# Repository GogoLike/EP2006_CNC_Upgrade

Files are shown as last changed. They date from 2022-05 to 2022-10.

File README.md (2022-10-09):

View this project on [CADLAB.io](https://cadlab.io/project/25653). 

## EP2006_CNC_Upgrade Project

# Описание проекта

Проект заключается в модернизации фрезерно-гравировально-сверлильного станка EP2006.
В качестве мождернизации подразумевается переход управления на стандарт G-Code с контроллером на открытой прошивке GRBL.
Контроллером в новой плате является STM32F103 в составе платы BluePill.

# Текущее состояние проекта

*Интерфейсы:*
- Известно управление исходным частотным преобразователем шпинделя
- Известно управление 5-ти фазными шаговыми двигателями через исходные драайвера шаговых двигателей осей X и Y
- Известно управление 2-х фазным шаговым двигателем через исходный драйвер шагового двигателя оси Z

*Датчики:*
- Известно подключение датчиков HOME
- Известно подключение датчика PROBE
- Выбрано подключение кнопки паузы на сигнал SAFETY_DOOR
- Выбрано подключение реле пылеососа на сигнал SPINDEL_ENABLE

*Схемотехника:*
- Коннектор для BluePill
- Датчики HOME заведены через оптопары и ферритовые кольца
- Управление X Y заведено через драйвер дифф. линий SN75ALS192N
- Управление Z заведено через инвертор SN7406N
- На Disable Steppers заведено только Enable Z

*PCB:*
- Реализовано на макетной плате

*Прошивка:*
- Удалось прошить контроллер
- В процессе настройки
- Проверена работоспособность движения по осям и перехода в HOME
- Проверен функционал щупа
- Проверено включение шпинделя
- Проверена резка плат

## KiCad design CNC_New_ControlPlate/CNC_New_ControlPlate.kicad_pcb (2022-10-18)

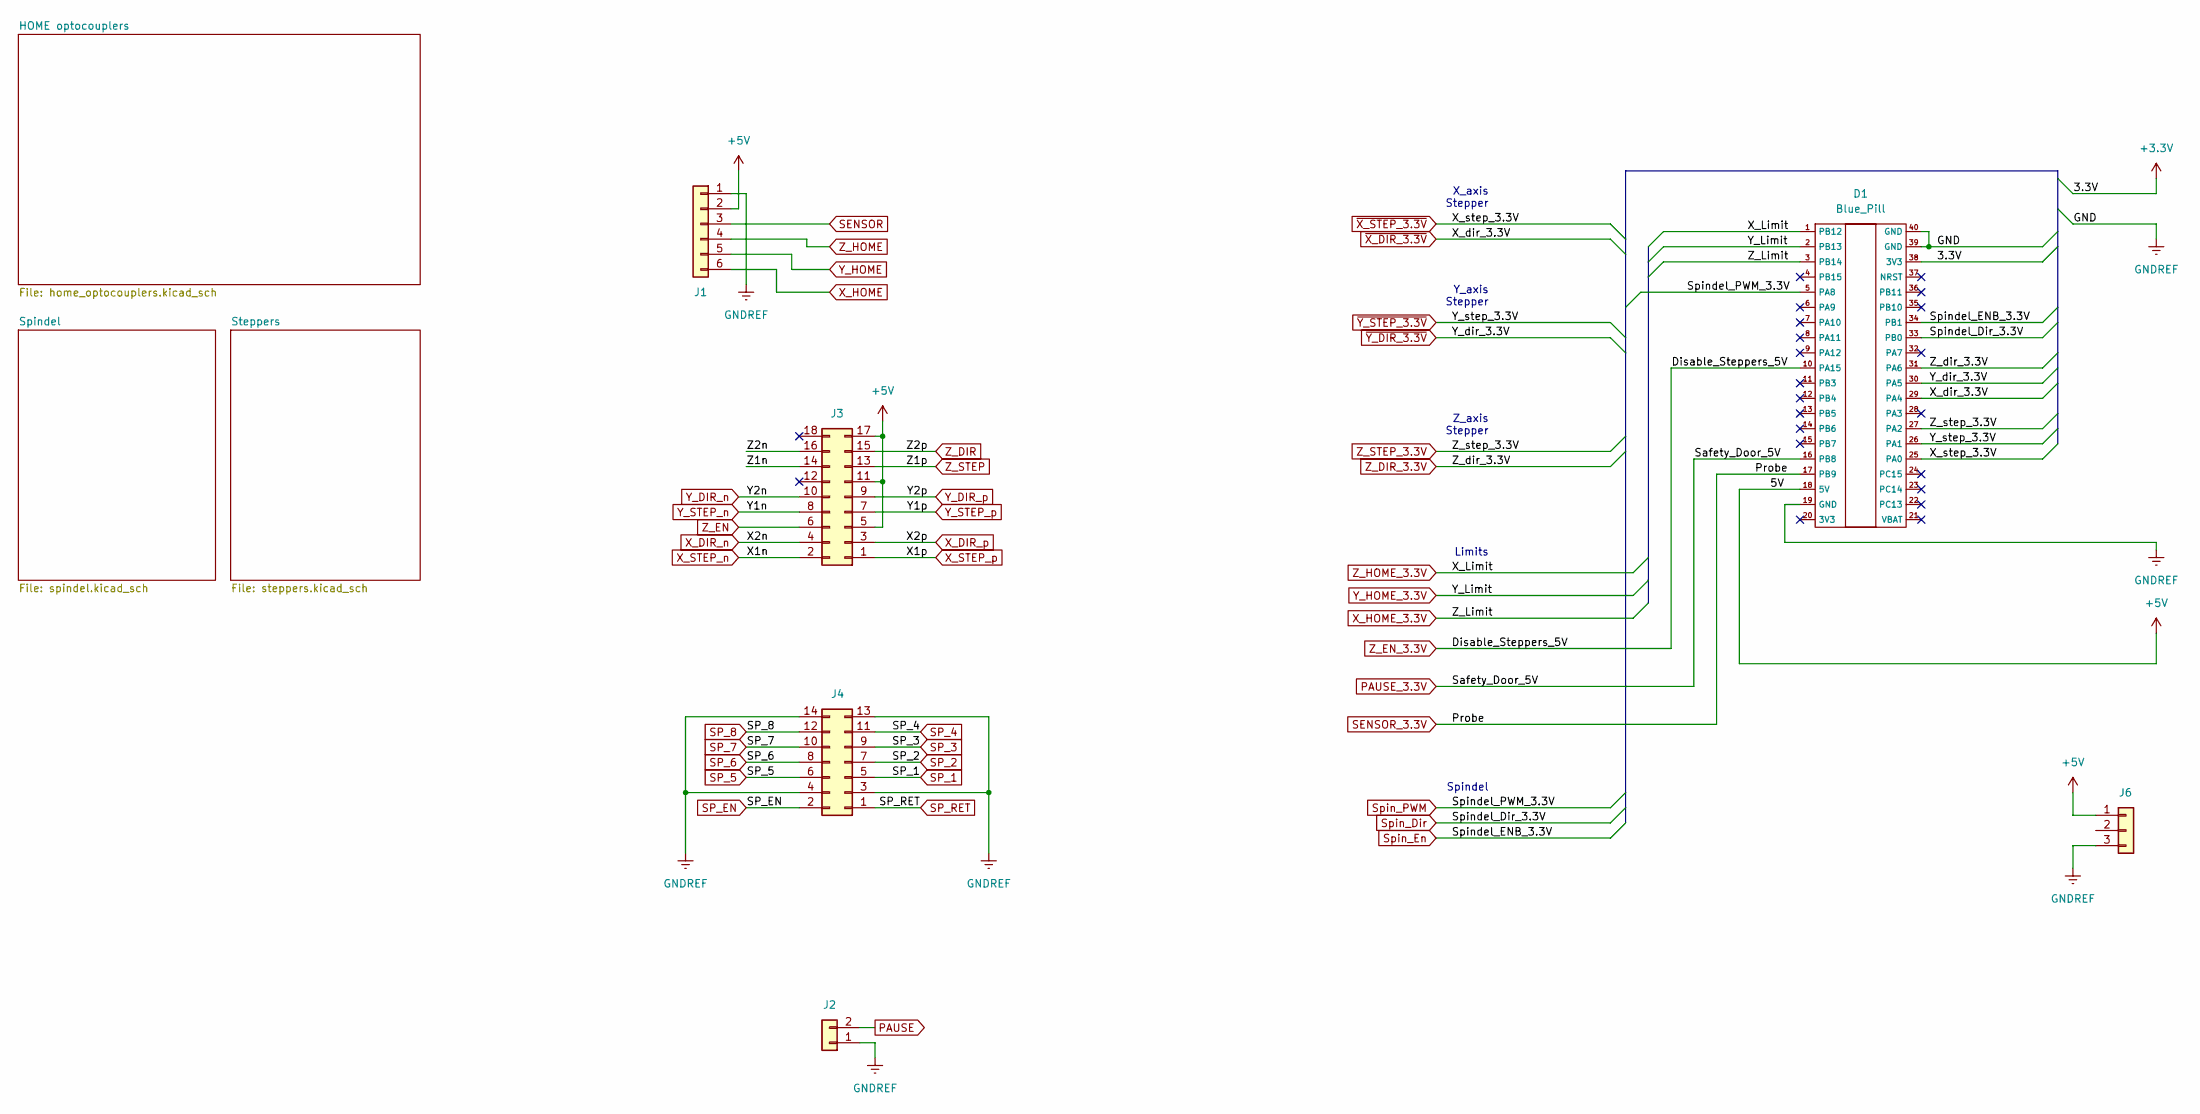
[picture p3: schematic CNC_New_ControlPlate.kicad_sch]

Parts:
D1: Blue_Pill; Maple_Mini
J1: OTHER; JST_XH_B6B-XH-A_1x06_P2.50mm_Vertical
J2: Conn_01x02; JST_XH_B2B-XH-A_1x02_P2.50mm_Vertical
J3: STEPPERS; PinHeader_2x09_P2.54mm_Vertical
J4: SPINDEL; PinHeader_2x07_P2.54mm_Vertical
J6: Conn_01x03; JST_VH_B3P-VH_1x03_P3.96mm_Vertical

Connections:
+3V3: D1.38 (3V3); also elsewhere on the board
+5V: D1.18 (5V), J1.2, J3.5, J3.11, J3.17, J6.1; also elsewhere on the board
/Z1n: J3.14
/Z2n: J3.16
GNDREF: D1.19 (GND), D1.39 (GND), D1.40 (GND), J1.1, J2.1, J4.3, J4.4, J4.13, J4.14, J6.3; also elsewhere on the board
PAUSE: J2.2; also elsewhere on the board
PAUSE_3.3V: D1.16 (PB8); also elsewhere on the board
SENSOR: J1.3; also elsewhere on the board
SENSOR_3.3V: D1.17 (PB9); also elsewhere on the board
SP_1: J4.5; also elsewhere on the board
SP_2: J4.7; also elsewhere on the board
SP_3: J4.9; also elsewhere on the board
SP_4: J4.11; also elsewhere on the board
SP_5: J4.6; also elsewhere on the board
SP_6: J4.8; also elsewhere on the board
SP_7: J4.10; also elsewhere on the board
SP_8: J4.12; also elsewhere on the board
SP_EN: J4.2; also elsewhere on the board
SP_RET: J4.1
Spin_Dir: D1.33 (PB0)
Spin_En: D1.34 (PB1); also elsewhere on the board
Spin_PWM: D1.5 (PA8); also elsewhere on the board
X_DIR_n: J3.4; also elsewhere on the board
X_DIR_p: J3.3; also elsewhere on the board
X_HOME: J1.6; also elsewhere on the board
X_HOME_3.3V: D1.3 (PB14); also elsewhere on the board
X_STEP_n: J3.2; also elsewhere on the board
X_STEP_p: J3.1; also elsewhere on the board
Y_DIR_n: J3.10; also elsewhere on the board
Y_DIR_p: J3.9; also elsewhere on the board
Y_HOME: J1.5; also elsewhere on the board
Y_HOME_3.3V: D1.2 (PB13); also elsewhere on the board
Y_STEP_n: J3.8; also elsewhere on the board
Y_STEP_p: J3.7; also elsewhere on the board
Z_DIR: J3.15; also elsewhere on the board
Z_DIR_3.3V: D1.31 (PA6); also elsewhere on the board
Z_EN: J3.6; also elsewhere on the board
Z_EN_3.3V: D1.10 (PA15); also elsewhere on the board
Z_HOME: J1.4; also elsewhere on the board
Z_HOME_3.3V: D1.1 (PB12); also elsewhere on the board
Z_STEP: J3.13; also elsewhere on the board
Z_STEP_3.3V: D1.27 (PA2); also elsewhere on the board
~X_DIR_3.3V: D1.29 (PA4); also elsewhere on the board
~X_STEP_3.3V: D1.25 (PA0); also elsewhere on the board
~Y_DIR_3.3V: D1.30 (PA5); also elsewhere on the board
~Y_STEP_3.3V: D1.26 (PA1); also elsewhere on the board

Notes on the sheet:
Spindel
Z_axis Stepper
Y_axis Stepper
X_axis Stepper
Limits

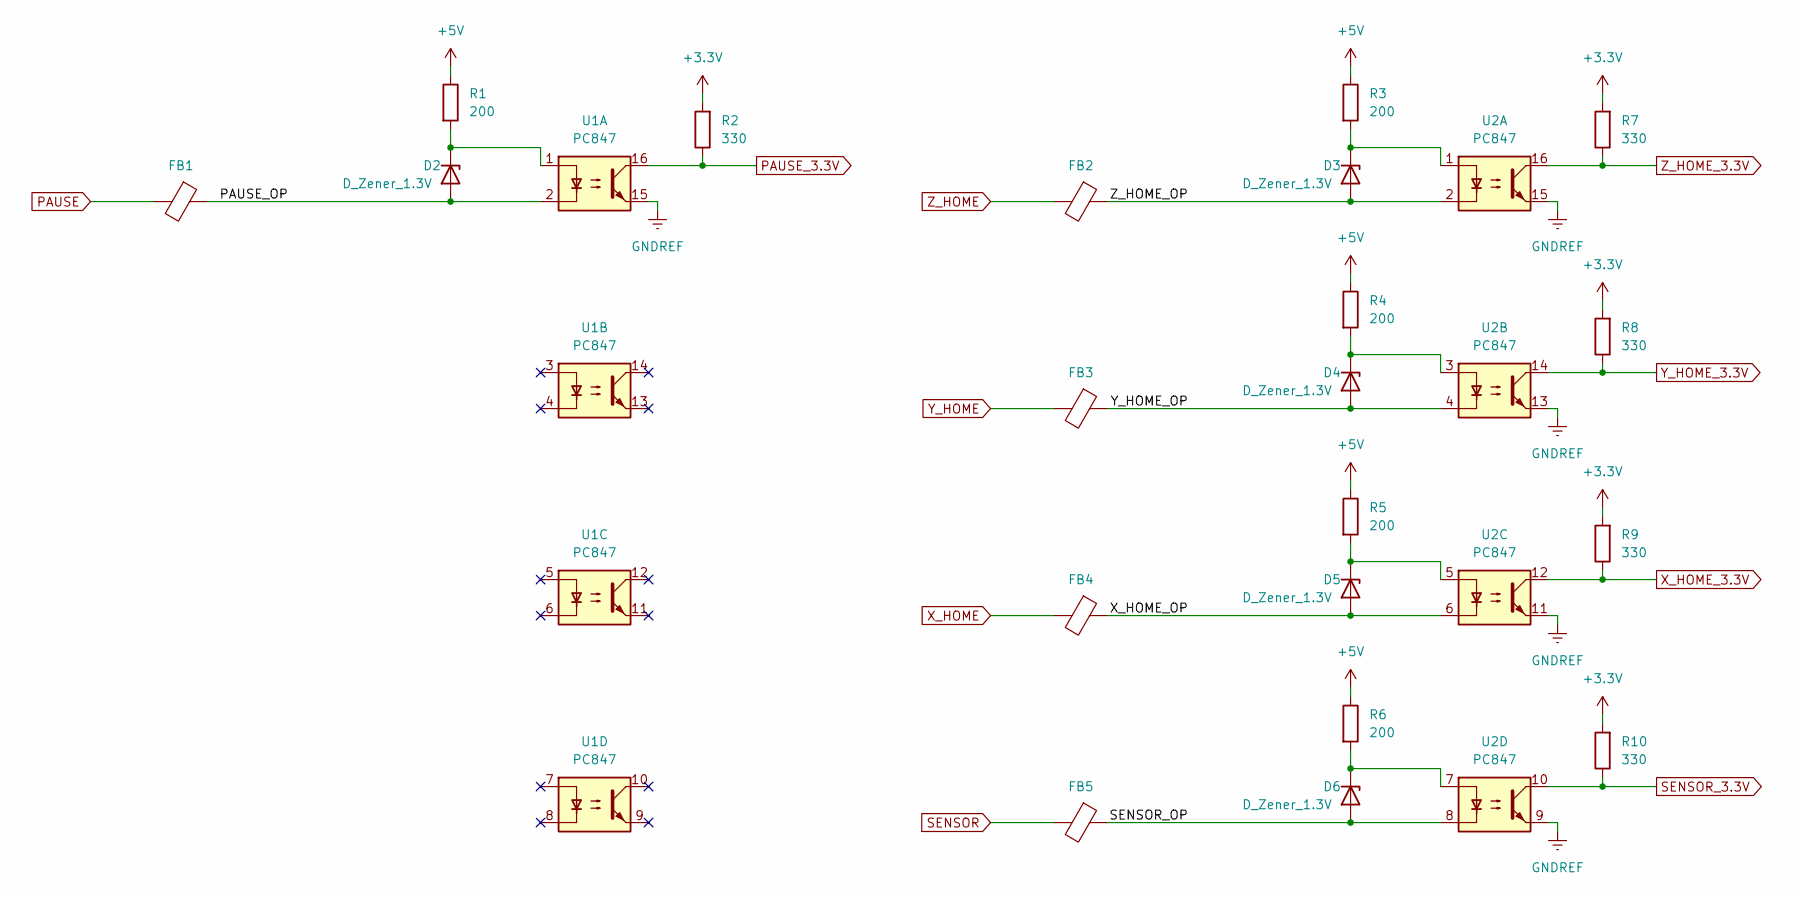
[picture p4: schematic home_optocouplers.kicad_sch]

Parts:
D2, D3, D4, D5, D6: D_Zener_1.3V; D_A-405_P7.62mm_Horizontal
FB1, FB2, FB3, FB4, FB5: FerriteBead; R_Axial_DIN0207_L6.3mm_D2.5mm_P7.62mm_Horizontal
R1, R3, R4, R5, R6: 200; R_0603_1608Metric
R2, R7, R8, R9, R10: 330; R_0603_1608Metric
U1, U2: PC847; DIP-16_W7.62mm_Socket_LongPads

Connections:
+3V3: R2.2, R7.2, R8.2, R9.2, R10.2; also elsewhere on the board
+5V: R1.1, R3.1, R4.1, R5.1, R6.1; also elsewhere on the board
/HOME optocouplers/PAUSE_OP: D2.2 (A), FB1.1, U1.2
/HOME optocouplers/SENSOR_OP: D6.2 (A), FB5.1, U2.8
/HOME optocouplers/X_HOME_OP: D5.2 (A), FB4.1, U2.6
/HOME optocouplers/Y_HOME_OP: D4.2 (A), FB3.1, U2.4
/HOME optocouplers/Z_HOME_OP: D3.2 (A), FB2.1, U2.2
GNDREF: U1.15, U2.9, U2.11, U2.13, U2.15; also elsewhere on the board
unnamed: D2.1 (K), R1.2, U1.1
unnamed: D3.1 (K), R3.2, U2.1
unnamed: D4.1 (K), R4.2, U2.3
unnamed: D5.1 (K), R5.2, U2.5
unnamed: D6.1 (K), R6.2, U2.7
PAUSE: FB1.2; also elsewhere on the board
PAUSE_3.3V: R2.1, U1.16; also elsewhere on the board
SENSOR: FB5.2; also elsewhere on the board
SENSOR_3.3V: R10.1, U2.10; also elsewhere on the board
X_HOME: FB4.2; also elsewhere on the board
X_HOME_3.3V: R9.1, U2.12; also elsewhere on the board
Y_HOME: FB3.2; also elsewhere on the board
Y_HOME_3.3V: R8.1, U2.14; also elsewhere on the board
Z_HOME: FB2.2; also elsewhere on the board
Z_HOME_3.3V: R7.1, U2.16; also elsewhere on the board

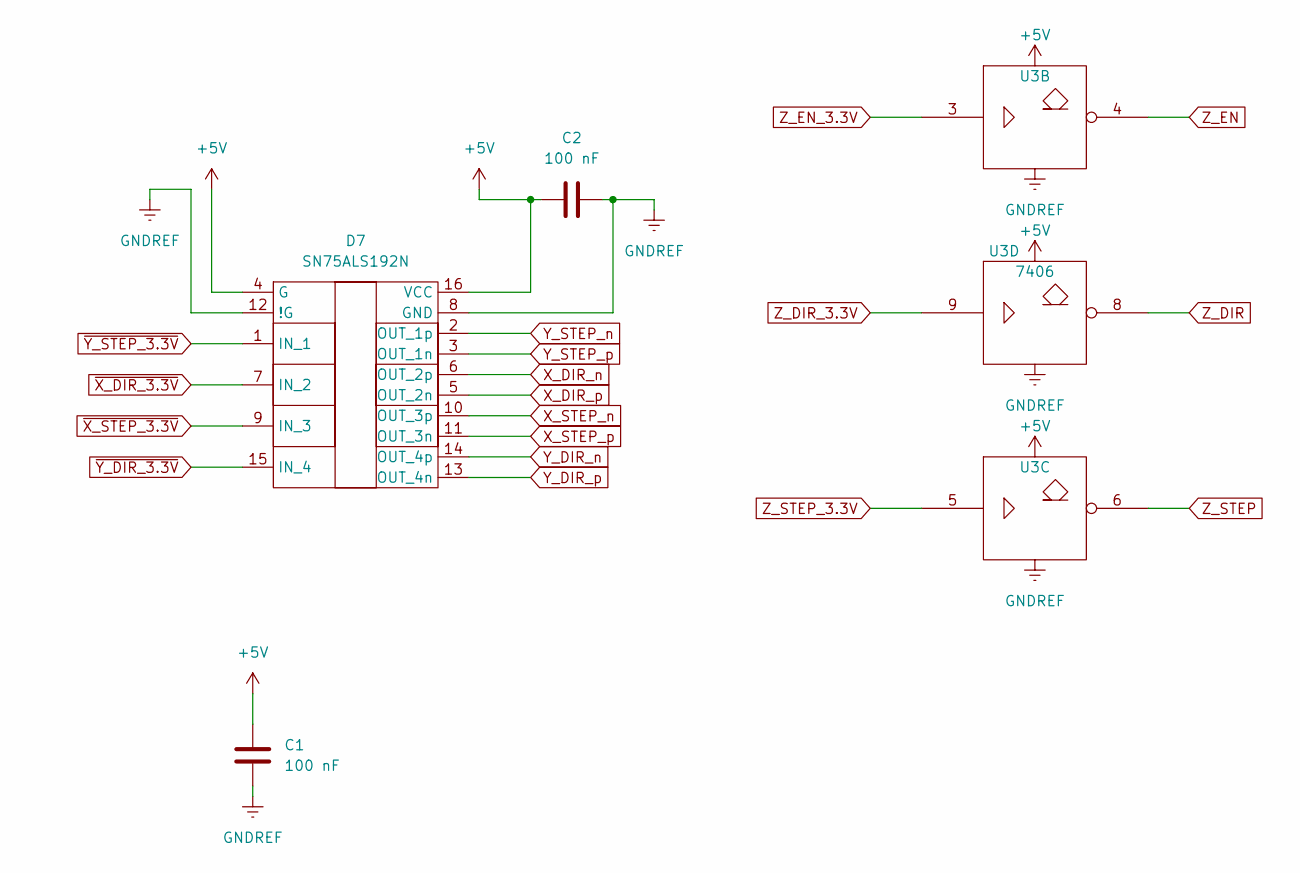
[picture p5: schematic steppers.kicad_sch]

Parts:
C1, C2: 100 nF; C_0603_1608Metric_Pad1.08x0.95mm_HandSolder
D7: SN75ALS192N; DIP-16_W7.62mm_Socket
U3: 7406; DIP-14_W7.62mm_Socket

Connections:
+5V: C1.2, C2.1, D7.4 (G), D7.16 (VCC), U3.14 (Vcc); also elsewhere on the board
GNDREF: C1.1, C2.2, D7.8 (GND), D7.12 (!G), U3.7 (Gnd); also elsewhere on the board
X_DIR_n: D7.6 (OUT_2p); also elsewhere on the board
X_DIR_p: D7.5 (OUT_2n); also elsewhere on the board
X_STEP_n: D7.10 (OUT_3p); also elsewhere on the board
X_STEP_p: D7.11 (OUT_3n); also elsewhere on the board
Y_DIR_n: D7.14 (OUT_4p); also elsewhere on the board
Y_DIR_p: D7.13 (OUT_4n); also elsewhere on the board
Y_STEP_n: D7.2 (OUT_1p); also elsewhere on the board
Y_STEP_p: D7.3 (OUT_1n); also elsewhere on the board
Z_DIR: U3.8; also elsewhere on the board
Z_DIR_3.3V: U3.9; also elsewhere on the board
Z_EN: U3.4; also elsewhere on the board
Z_EN_3.3V: U3.3; also elsewhere on the board
Z_STEP: U3.6; also elsewhere on the board
Z_STEP_3.3V: U3.5; also elsewhere on the board
~X_DIR_3.3V: D7.7 (IN_2); also elsewhere on the board
~X_STEP_3.3V: D7.9 (IN_3); also elsewhere on the board
~Y_DIR_3.3V: D7.15 (IN_4); also elsewhere on the board
~Y_STEP_3.3V: D7.1 (IN_1); also elsewhere on the board

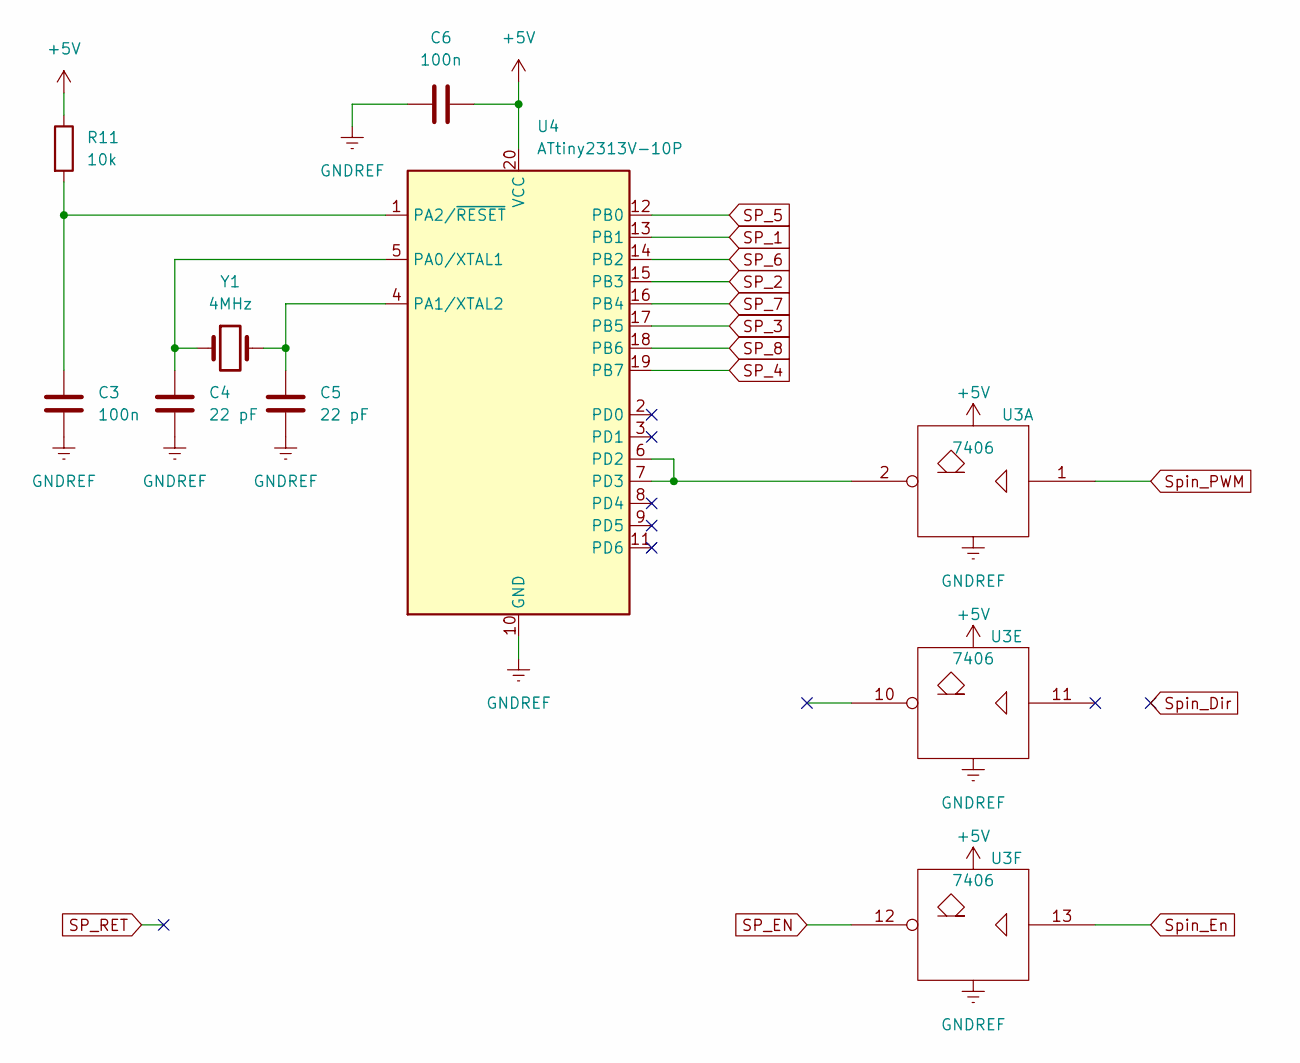
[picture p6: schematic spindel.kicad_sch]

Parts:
C3, C6: 100n; C_0603_1608Metric_Pad1.08x0.95mm_HandSolder
C4, C5: 22 pF; C_0603_1608Metric_Pad1.08x0.95mm_HandSolder
R11: 10k; R_0603_1608Metric
U3: 7406; DIP-14_W7.62mm_Socket
U4: ATtiny2313V-10P; DIP-20_W7.62mm
Y1: 4MHz; Crystal_HC49-4H_Vertical

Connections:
+5V: C6.2, R11.1, U3.14 (Vcc), U4.20 (VCC); also elsewhere on the board
GNDREF: C3.1, C4.1, C5.1, C6.1, U3.7 (Gnd), U4.10 (GND); also elsewhere on the board
unnamed: C3.2, R11.2, U4.1 (PA2/~RESET)
unnamed: C4.2, U4.5 (PA0/XTAL1), Y1.1
unnamed: C5.2, U4.4 (PA1/XTAL2), Y1.2
unnamed: U3.2, U4.6 (PD2), U4.7 (PD3)
SP_1: U4.13 (PB1); also elsewhere on the board
SP_2: U4.15 (PB3); also elsewhere on the board
SP_3: U4.17 (PB5); also elsewhere on the board
SP_4: U4.19 (PB7); also elsewhere on the board
SP_5: U4.12 (PB0); also elsewhere on the board
SP_6: U4.14 (PB2); also elsewhere on the board
SP_7: U4.16 (PB4); also elsewhere on the board
SP_8: U4.18 (PB6); also elsewhere on the board
SP_EN: U3.12; also elsewhere on the board
Spin_En: U3.13; also elsewhere on the board
Spin_PWM: U3.1; also elsewhere on the board

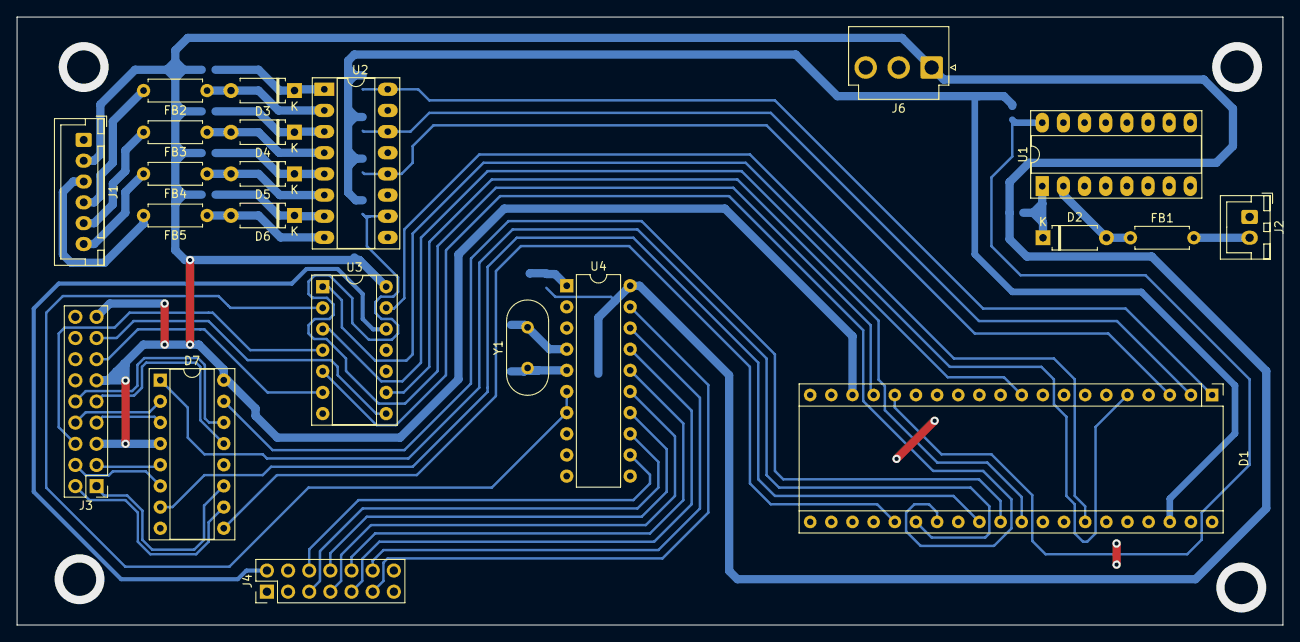
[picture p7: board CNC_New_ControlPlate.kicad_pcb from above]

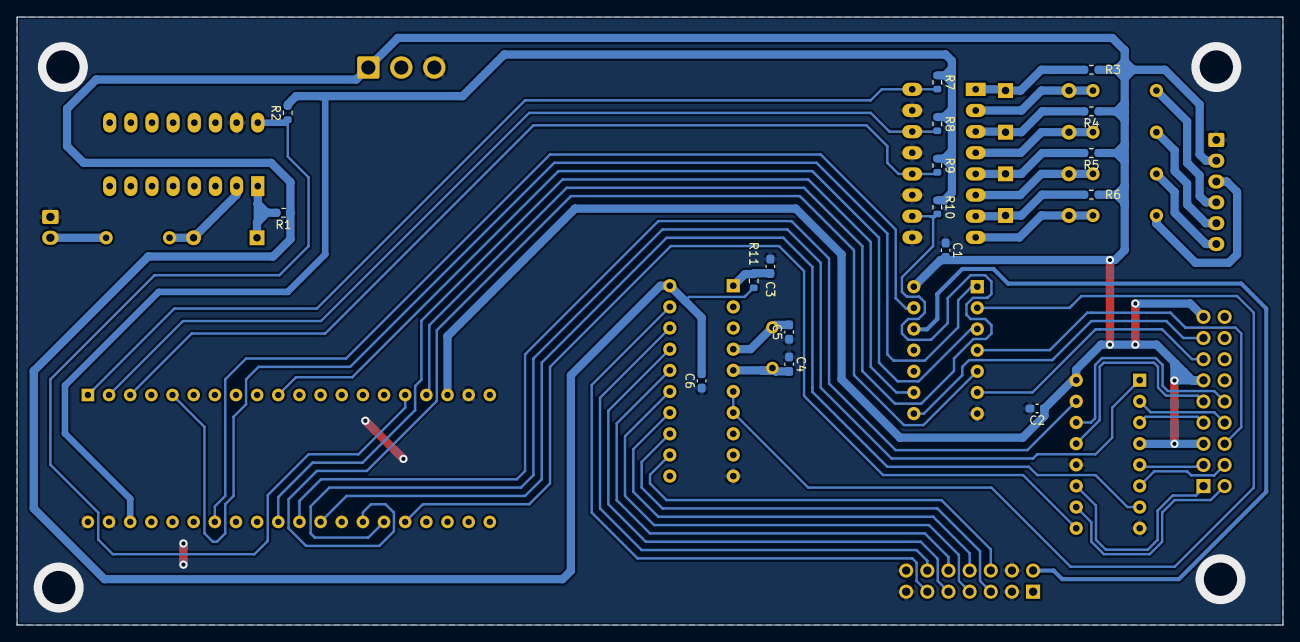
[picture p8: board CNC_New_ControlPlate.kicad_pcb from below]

Board: 2 copper layers, 152.0 x 73.0 mm, 39 parts (17 on the bottom side), 56 nets.

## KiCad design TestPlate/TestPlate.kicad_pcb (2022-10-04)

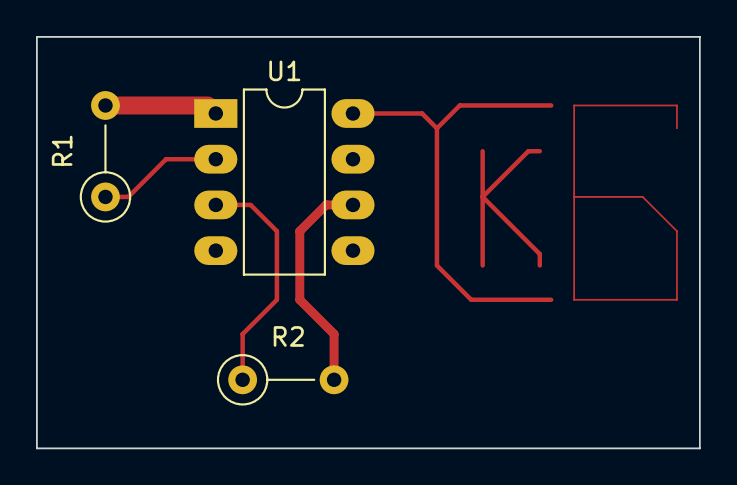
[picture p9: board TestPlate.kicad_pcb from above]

Board: 2 copper layers, 36.8 x 22.9 mm, 3 parts (0 on the bottom side), 4 nets.

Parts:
R1, R2: R; R_Axial_DIN0207_L6.3mm_D2.5mm_P5.08mm_Vertical
U1: 4555; DIP-8_W7.62mm_LongPads

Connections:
unnamed: R1.1, U1.2 (A0)
unnamed: R1.2, U1.1 (~EN)
unnamed: R2.1, U1.3 (A1)
unnamed: R2.2, U1.6 (Q2)

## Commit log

2022-05-23 Create Repo
    [CNC_New_ControlPlate.kicad_pcb, CNC_New_ControlPlate.kicad_sch]
2022-05-23 Cancel Test
    [CNC_New_ControlPlate.kicad_sch]
2022-05-24 + Интерфейс STM32F103
    Доделал выводы на глобальные метки всех необходимых GRBL контактов
    [CNC_New_ControlPlate.kicad_sch]
2022-05-24 Взял в работу заведение датчиков HOME через оптопары
2022-05-24 +Файл линий HOME и SENSOR
    + Завел датчики через оптопары
    + Посчитал токоограничивающие резисторы на вход и выход оптопары
    + Поставил стабилитроны, возможно не понадобятся
    [CNC_New_ControlPlate.kicad_sch, home_optocouplers.kicad_sch]
2022-05-28 Датчики и щуп через оптопары
    [CNC_New_ControlPlate.kicad_sch, home_optocouplers.kicad_sch]
2022-09-08 [*] ReadME [+] Даташиты на драйверы шаговых двигателей
2022-09-17 Обновил датчики HOME
    [CNC_New_ControlPlate.kicad_sch, home_optocouplers.kicad_sch]
2022-09-17 [+] Лист STEPPERS [+] Разъем подключения шаговиков [+] Моделька драйвера дифф линий [+] Управление X Y заведено через драйверы дифф линий [+] Управление Z заведено через инвертор [+] Enable Z заведен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
    [CNC_New_ControlPlate.kicad_sch, home_optocouplers.kicad_sch, steppers.kicad_sch]
2022-09-20 Add GRBL submodule
2022-10-04 Add test plate
    [TestPlate.kicad_pcb, TestPlate.kicad_sch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]
2022-10-09 Add spindel sch
    [CNC_New_ControlPlate.kicad_sch, home_optocouplers.kicad_sch, steppers.kicad_sch]
2022-10-11 Add attiny2313
    [CNC_New_ControlPlate.kicad_sch, steppers.kicad_sch]
2022-10-11 Add attiny2313 2
    [CNC_New_ControlPlate.kicad_sch]
2022-10-11 Add spindel
    [spindel.kicad_sch]
2022-10-11 [*] номиналы блокировочных конденсаторов [+] мкроконтроллер управления оборотами шпинделя [+] кнопка паузы
    [CNC_New_ControlPlate.kicad_sch, home_optocouplers.kicad_sch, spindel.kicad_sch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]
2022-10-12 Cosmetic edit
    [CNC_New_ControlPlate.kicad_sch, home_optocouplers.kicad_sch, spindel.kicad_sch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]
2022-10-12 [*] Исправлены ошибки с выходами питания. [+] Добавлены обозначения элементов
    [CNC_New_ControlPlate.kicad_sch, home_optocouplers.kicad_sch, spindel.kicad_sch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]
2022-10-12 [*] Порядок выводов на разъёме Others [*] Порядок выводов на разъёме Pause [*] Порядок подключения каналов на драйвере диф. линий [+] Начата расстановка pcb схемы
    [CNC_New_ControlPlate.kicad_pcb, CNC_New_ControlPlate.kicad_sch, spindel.kicad_sch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]
2022-10-13 Edit footprints
    [CNC_New_ControlPlate.kicad_sch, home_optocouplers.kicad_sch, spindel.kicad_sch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]
2022-10-15 [*] Разводка платы в один слой (осталось 7 перемычек)
    [CNC_New_ControlPlate.kicad_pcb, CNC_New_ControlPlate.kicad_sch, home_optocouplers.kicad_sch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]
2022-10-15 Edit PCB, add jumpers
    [CNC_New_ControlPlate.kicad_pcb]
2022-10-15 [*] Разведена плата в один слой (3 перемычки на шине 5В; 2 соединения земли через плату STM
    [CNC_New_ControlPlate.kicad_pcb, CNC_New_ControlPlate.kicad_sch, home_optocouplers.kicad_sch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]
2022-10-18 [+] Добавлен разъем питания
    [CNC_New_ControlPlate.kicad_pcb, CNC_New_ControlPlate.kicad_sch]
